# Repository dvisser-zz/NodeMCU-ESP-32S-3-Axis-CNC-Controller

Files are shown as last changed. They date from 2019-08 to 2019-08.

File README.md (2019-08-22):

# NodeMCU-ESP-32S-3-Axis-CNC-Controller

## 3-Axis CNC Controller using Trinamic TMC5160 drivers.

### Runs the GRBL-ESP32 firmware by bdring found here https://github.com/bdring/Grbl_Esp32/tree/TMCStepper

###### Board Specifications:

- 24V DC nominal motor/board supply voltage 
  - Working Range
    - 18V DC (min)
    - 36V DC (max)
- Based on ESP32 MCU
- 3 x stepper drivers (TMC5160) to suit 3-axis machines
- Multiple spindle control options 
  - 3.3V PWM output
  - 0-5V analog DC output
  - 0-10V analog DC output (op-amp buffered)
  - 3.3V spindle enable binary output (works with 5v logic VFD binary inputs as well)
- Z Probe input (3.3V logic level)
- All screw terminals are 5.08mm pitch for reliability and durability
- On-board micro SD card support
- Spindle Coolant Relay (active when spindle is enabled) with LED indicator
- Tool/Cutting Coolant Relay (active with grbl mist output is enabled) with LED indicator
- 3 x power LED's (3.3V, 5V and 24V)

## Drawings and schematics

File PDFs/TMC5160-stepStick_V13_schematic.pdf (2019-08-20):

# GND GND GND GND ²²nF

1

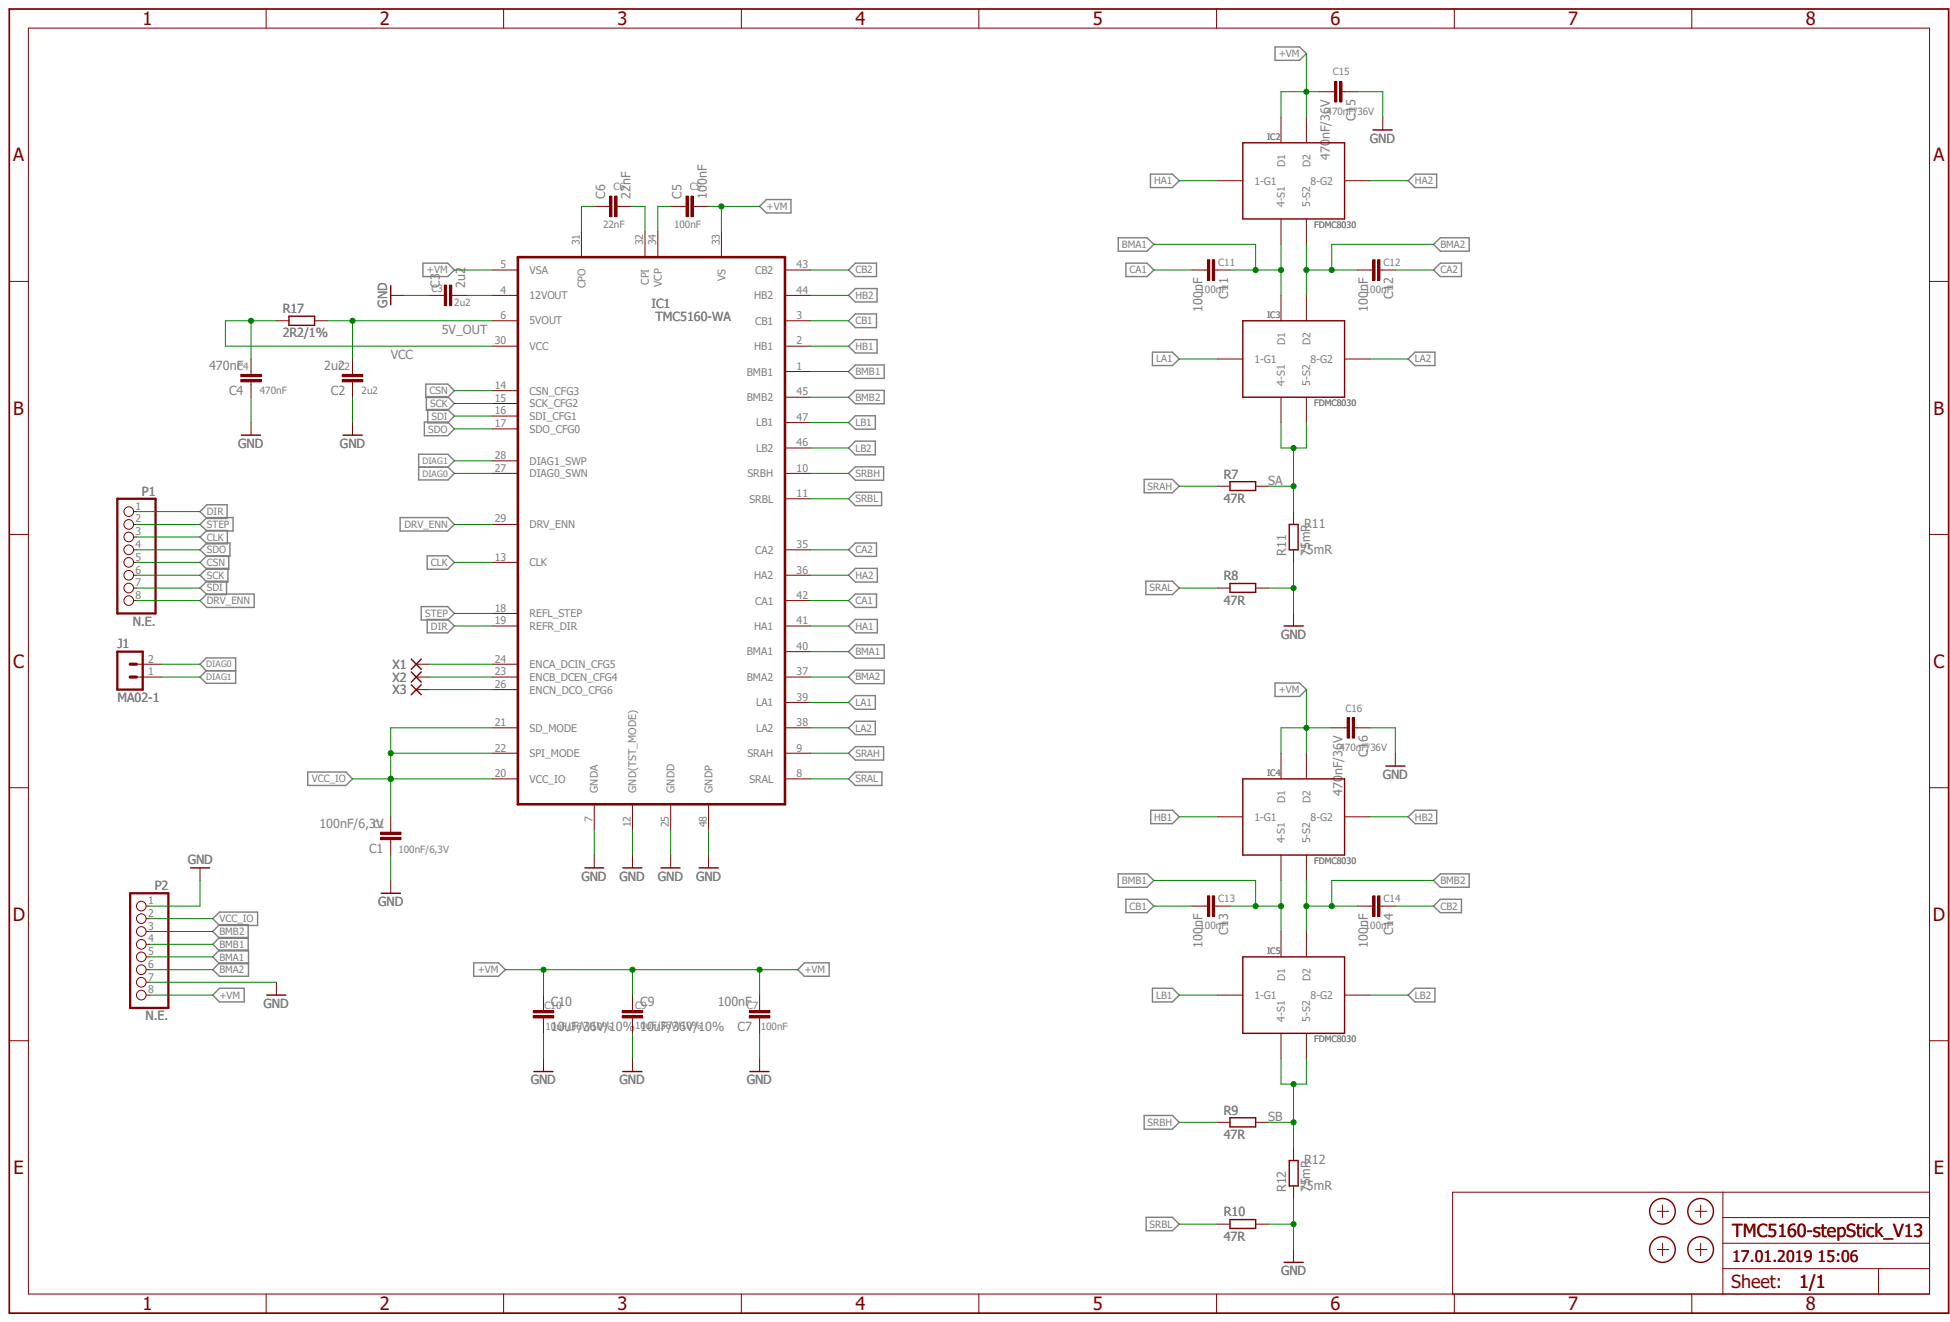
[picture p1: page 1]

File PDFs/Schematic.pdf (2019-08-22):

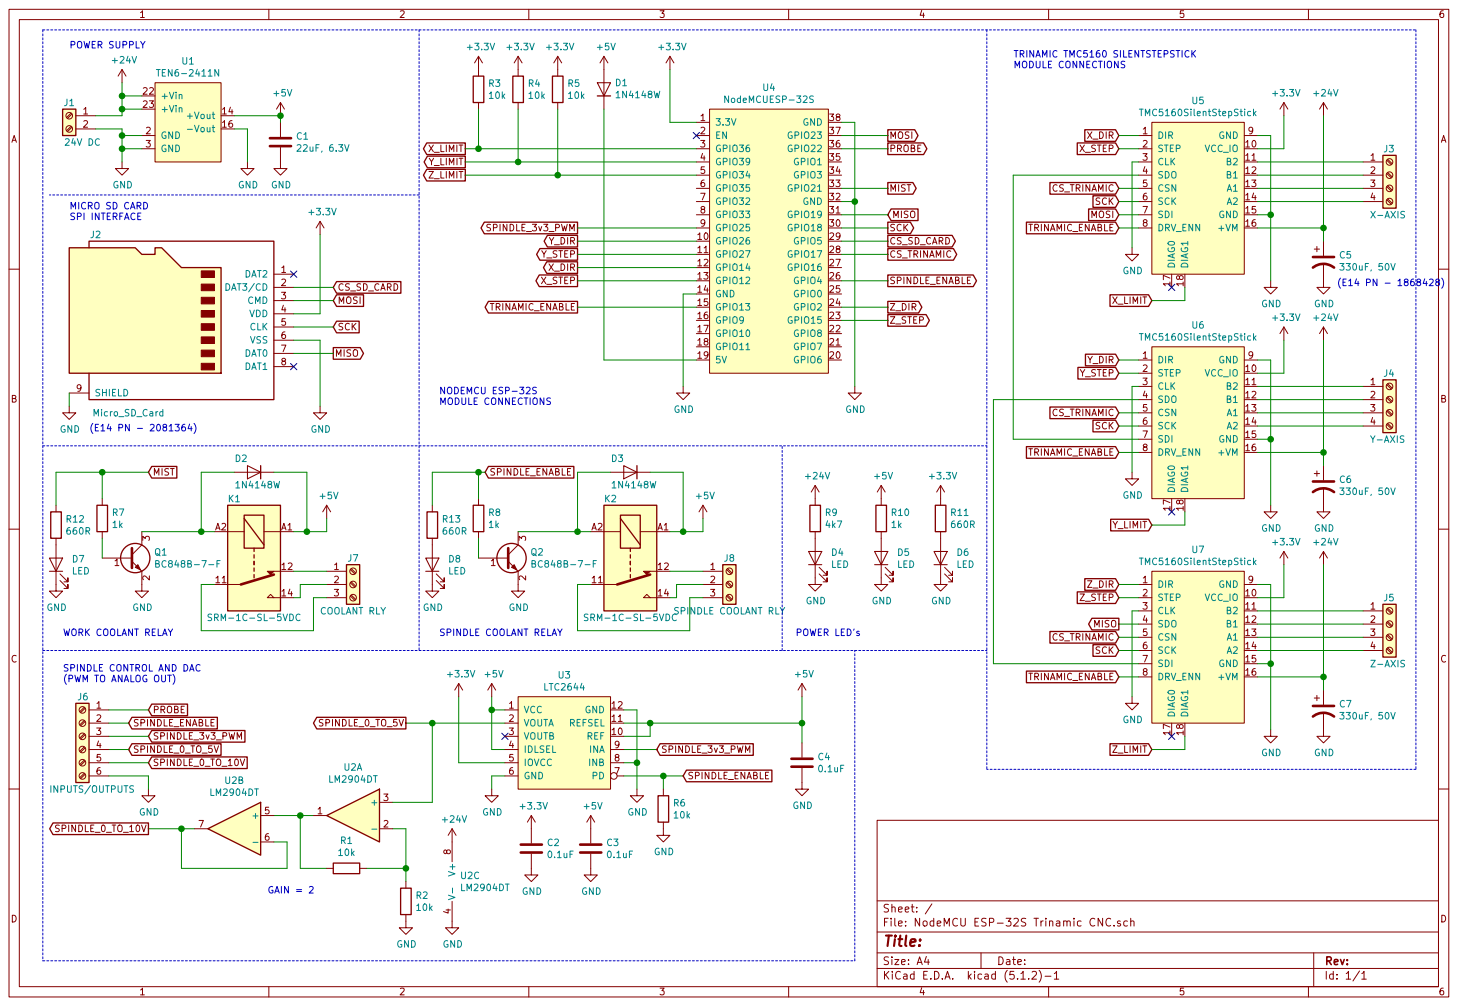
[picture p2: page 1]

TRINAMIC TMC5160 SILENTSTEPSTICK MODULE CONNECTIONS

NODEMCU ESP-32S MODULE CONNECTIONS

CS_TRINAMIC SCK | | 3

Id: 1/1 Title: File: NodeMCU ESP-32S Trinamic CNC.sch Sheet: /

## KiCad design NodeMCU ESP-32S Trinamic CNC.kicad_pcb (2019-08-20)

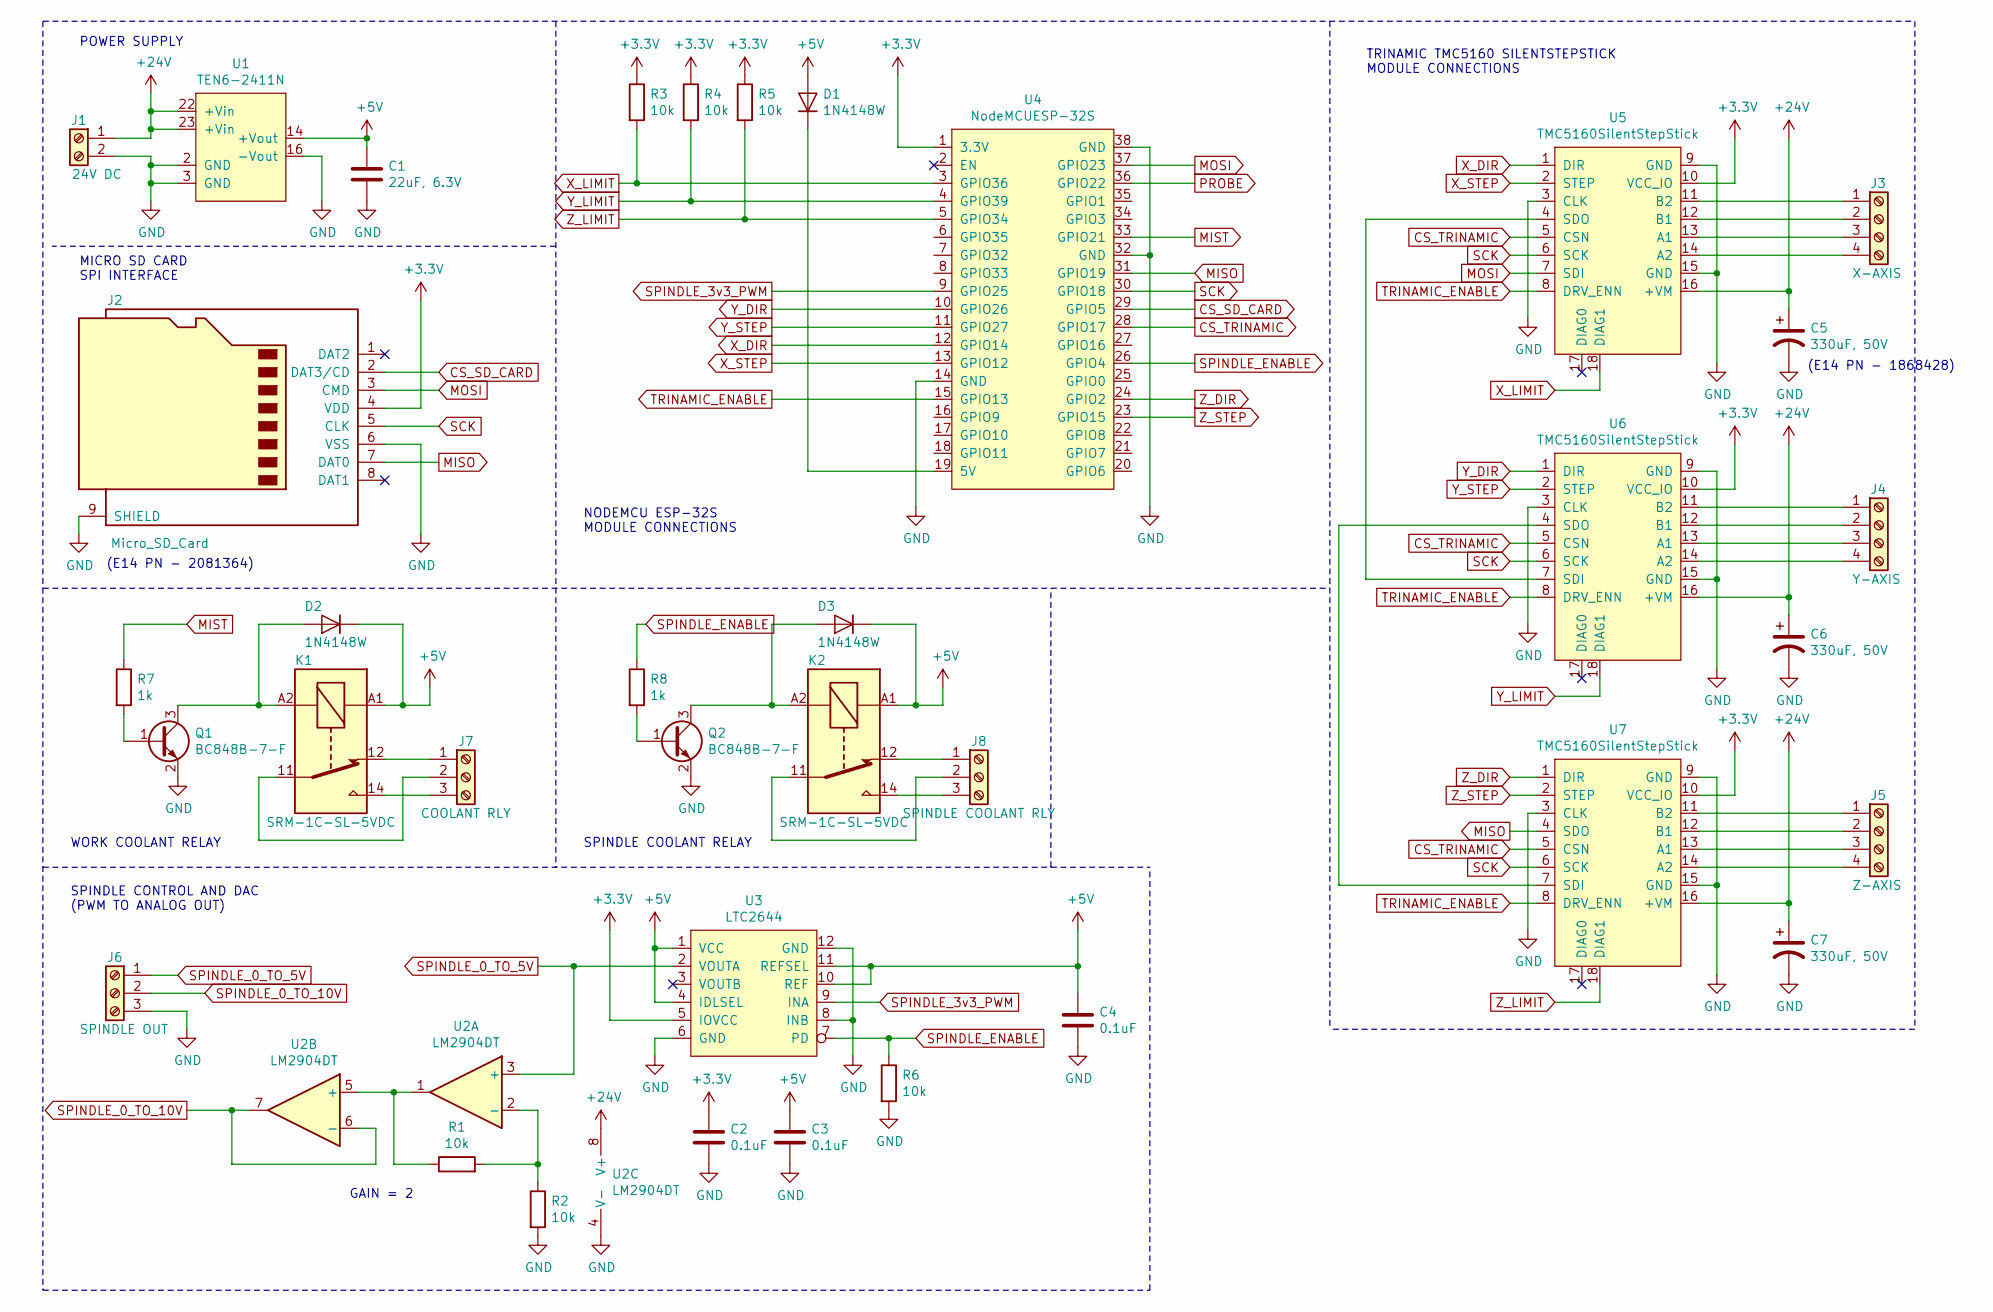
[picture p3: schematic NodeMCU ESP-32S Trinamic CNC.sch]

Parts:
C1: 22uF, 6.3V; C_0603_1608Metric
C2, C3, C4: 0.1uF; C_0603_1608Metric
C5, C6, C7: 330uF, 50V; CP_Elec_10x10.5
D1, D2, D3: 1N4148W; D_SOD-123
J1: 24V DC; TerminalBlock_bornier-2_P5.08mm
J2: Micro_SD_Card; microSD_HC_Wuerth_693072010801
J3: X-AXIS; TerminalBlock_bornier-4_P5.08mm
J4: Y-AXIS; TerminalBlock_bornier-4_P5.08mm
J5: Z-AXIS; TerminalBlock_bornier-4_P5.08mm
J6: SPINDLE OUT; TerminalBlock_bornier-3_P5.08mm
J7: COOLANT RLY; TerminalBlock_bornier-3_P5.08mm
J8: SPINDLE COOLANT RLY; TerminalBlock_bornier-3_P5.08mm
K1, K2: SRM-1C-SL-5VDC
Q1, Q2: BC848B-7-F; SOT-23
R1, R2, R3, R4, R5, R6: 10k; R_0603_1608Metric
R7, R8: 1k; R_0603_1608Metric
U1: TEN6-2411N
U2: LM2904DT; SO-8_3.9x4.9mm_P1.27mm
U3: LTC2644; MSOP-12_3x4mm_P0.65mm
U4: NodeMCUESP-32S
U5, U6, U7: TMC5160SilentStepStick

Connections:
+3V3: C2.1, J2.4 (VDD), R3.1, R4.1, R5.1, U3.5 (IOVCC), U4.1 (3.3V), U5.10 (VCC_IO), U6.10 (VCC_IO), U7.10 (VCC_IO)
+5V: C1.1, C3.1, C4.1, D1.2 (A), D2.1 (K), D3.1 (K), K1.A1, K2.A1, U1.14 (+Vout), U3.1 (VCC), U3.4 (IDLSEL), U3.10 (REF), U3.11 (REFSEL)
+24V: C5.1, C6.1, C7.1, J1.1, U1.22 (+Vin), U1.23 (+Vin), U2.8 (V+), U5.16 (+VM), U6.16 (+VM), U7.16 (+VM)
CS_SD_CARD: J2.2 (DAT3/CD), U4.29 (GPIO5)
CS_TRINAMIC: U4.28 (GPIO17), U5.5 (CSN), U6.5 (CSN), U7.5 (CSN)
GND: C1.2, C2.2, C3.2, C4.2, C5.2, C6.2, C7.2, J1.2, J2.6 (VSS), J2.9 (SHIELD), J6.3, Q1.2 (E), Q2.2 (E), R2.2, R6.2, U1.2 (GND), U1.3 (GND), U1.16 (-Vout), U2.4 (V-), U3.6 (GND), U3.8 (INB), U3.12 (GND), U4.14 (GND), U4.32 (GND), U4.38 (GND), U5.3 (CLK), U5.9 (GND), U5.15 (GND), U6.3 (CLK), U6.9 (GND), U6.15 (GND), U7.3 (CLK), U7.9 (GND), U7.15 (GND)
MISO: J2.7 (DAT0), U4.31 (GPIO19), U7.4 (SDO)
MIST: R7.1, U4.33 (GPIO21)
MOSI: J2.3 (CMD), U4.37 (GPIO23), U5.7 (SDI)
unnamed: D1.1 (K), U4.19 (5V)
unnamed: D2.2 (A), K1.A2, Q1.3 (C)
unnamed: D3.2 (A), K2.A2, Q2.3 (C)
unnamed: J3.1, U5.11 (B2)
unnamed: J3.2, U5.12 (B1)
unnamed: J3.3, U5.13 (A1)
unnamed: J3.4, U5.14 (A2)
unnamed: J4.1, U6.11 (B2)
unnamed: J4.2, U6.12 (B1)
unnamed: J4.3, U6.13 (A1)
unnamed: J4.4, U6.14 (A2)
unnamed: J5.1, U7.11 (B2)
unnamed: J5.2, U7.12 (B1)
unnamed: J5.3, U7.13 (A1)
unnamed: J5.4, U7.14 (A2)
unnamed: J7.1, K1.12
unnamed: J7.2, K1.11
unnamed: J7.3, K1.14
unnamed: J8.1, K2.12
unnamed: J8.2, K2.11
unnamed: J8.3, K2.14
unnamed: Q1.1 (B), R7.2
unnamed: Q2.1 (B), R8.2
unnamed: R1.1, U2.1, U2.5 (+)
unnamed: R1.2, R2.1, U2.2 (-)
unnamed: U5.4 (SDO), U6.7 (SDI)
unnamed: U6.4 (SDO), U7.7 (SDI)
PROBE: U4.36 (GPIO22)
SCK: J2.5 (CLK), U4.30 (GPIO18), U5.6 (SCK), U6.6 (SCK), U7.6 (SCK)
SPINDLE_0_TO_5V: J6.1, U2.3 (+), U3.2 (VOUTA)
SPINDLE_0_TO_10V: J6.2, U2.6 (-), U2.7
SPINDLE_3v3_PWM: U3.9 (INA), U4.9 (GPIO25)
SPINDLE_ENABLE: R6.1, R8.1, U3.7 (PD), U4.26 (GPIO4)
TRINAMIC_ENABLE: U4.15 (GPIO13), U5.8 (DRV_ENN), U6.8 (DRV_ENN), U7.8 (DRV_ENN)
X_DIR: U4.12 (GPIO14), U5.1 (DIR)
X_LIMIT: R3.2, U4.3 (GPIO36), U5.18 (DIAG1)
X_STEP: U4.13 (GPIO12), U5.2 (STEP)
Y_DIR: U4.10 (GPIO26), U6.1 (DIR)
Y_LIMIT: R4.2, U4.4 (GPIO39), U6.18 (DIAG1)
Y_STEP: U4.11 (GPIO27), U6.2 (STEP)
Z_DIR: U4.24 (GPIO2), U7.1 (DIR)
Z_LIMIT: R5.2, U4.5 (GPIO34), U7.18 (DIAG1)
Z_STEP: U4.23 (GPIO15), U7.2 (STEP)

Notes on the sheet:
GAIN = 2
SPINDLE CONTROL AND DAC (PWM TO ANALOG OUT)
(E14 PN - 2081364)
MICRO SD CARD SPI INTERFACE
NODEMCU ESP-32S MODULE CONNECTIONS
POWER SUPPLY
TRINAMIC TMC5160 SILENTSTEPSTICK MODULE CONNECTIONS
(E14 PN - 1868428)
WORK COOLANT RELAY
SPINDLE COOLANT RELAY

Board: 2 copper layers, 37 parts (0 on the bottom side), 51 nets, no tracks yet.

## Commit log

2019-08-22 First release with gerber files included.
    [NodeMCU ESP-32S Trinamic CNC.sch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]
2019-08-22 Updated PDF schematic.
